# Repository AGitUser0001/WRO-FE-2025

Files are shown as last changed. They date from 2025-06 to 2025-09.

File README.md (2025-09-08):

# WRO-FE-2025
Our repository for the 2025 World Robot Olympiad - Future Engineers.

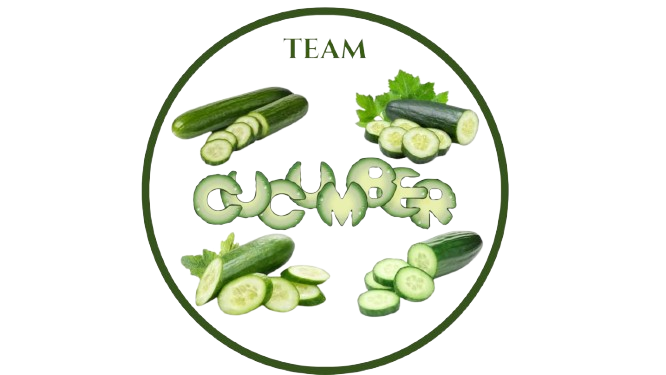
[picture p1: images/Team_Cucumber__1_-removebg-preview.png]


Team Name: Team Cucumber

This repository contains information about our robot and the building process. 

## Links
- [Building Instructions](/Building-Instructions.md)
- [Software Documentation](/Software-Documentation.md)
- [Open Challenge Documentation](/Software-Documentation.md#open-challenge)
- [Obstacle Challenge Documentation](/Software-Documentation.md#obstacle-management)

## Table of Contents
* [The Team](#team)
* [The Challenge](#challenge)
* [The Robot](#robot-image)
  * [First Design](#first)
  * [Final Design](#final)
* [Performance Videos](#video)
  * [Open challenge](#OPCV)
  * [Obstacle Challenge](#OBCV)  
* [Management](#management)
  * [Mobility Management](#mobility-management)
      * [Motor](#motor)
      * [Servo Motor](#servo-motor)
      * [Wheels](#wheels)
  * [Power and Sense Management](#power-and-sense-management)
    * [Battery](#battery)
    * [Raspi Camera](#camera)
    * [LiDAR](#lidar)
    * [Raspberry Pi 5](#pi)
    * [Expansion Board](#expansion-board)
    * [Circuit Diagram](#circuit-diagram)
* [Total Cost](#cost-report)
* [Future Potential Improvements](#potential-improvements)

## Team Members 

### Lucas Zheng
**Age:** 14

**Introduction:**
Hello, I'm Lucas, and this is my first time competing in WRO. I'm from Canada and 14 years old. I'm interested in coding and mathematics. It is my first year of high school at Donald A. Wilson Secondary School. I was interested in WRO Future Engineers because it has hardware and software aspects.
### Walter Wu
**Age:** 14

**Introduction:**
Hi, my name is Walter and I'm from Canada, this is my second WRO season, two years ago I participated in WRO Robo mission and ended up on the international stage in Panama. This year since I was old enough for future engineers I decided to sign up for a completely different challenge, I am currently 14 years old and I have many interests from coding to a variety of video games and sports, I will be attending All saints catholic secondary school for their AMP program.
### Eric Huang
**Age:** 15

**Introduction:**
Hello, I'm Eric, and I have already participated in two WRO competitions so far. Although I have not entered the international stage in any of them, I believe these competitions helped me better problem solve and gave me something to do. This is also why I am participating in Future Engineers this year. My interests are chess, badminton, and swimming. 
## Our coach

### Rice Rao
<table>
  <tr>
    <td width="50%" style="text-align: left;">
       
    </td>
    <td width="50%" style="text-align: left; vertical-align: top;">
      <h3>Achievements:</h3>
      <ul>
        <li>Head coach of Robotics Competitions including FLL (First LEGO League) Tournament and WRO (World Robotics Olympiad). Led teams in winning multiple national, international robotics and programming awards.</li>
        <li>Over 20 years of IT industry experience as software engineer working internationally.</li>
        <li>MSc in Electrical & Computer Engineering from University of Alberta.</li>
        <li>BSc in Mathematics from Peking University.</li>
      </ul>
    </td>
  </tr>
</table>

## Group photo
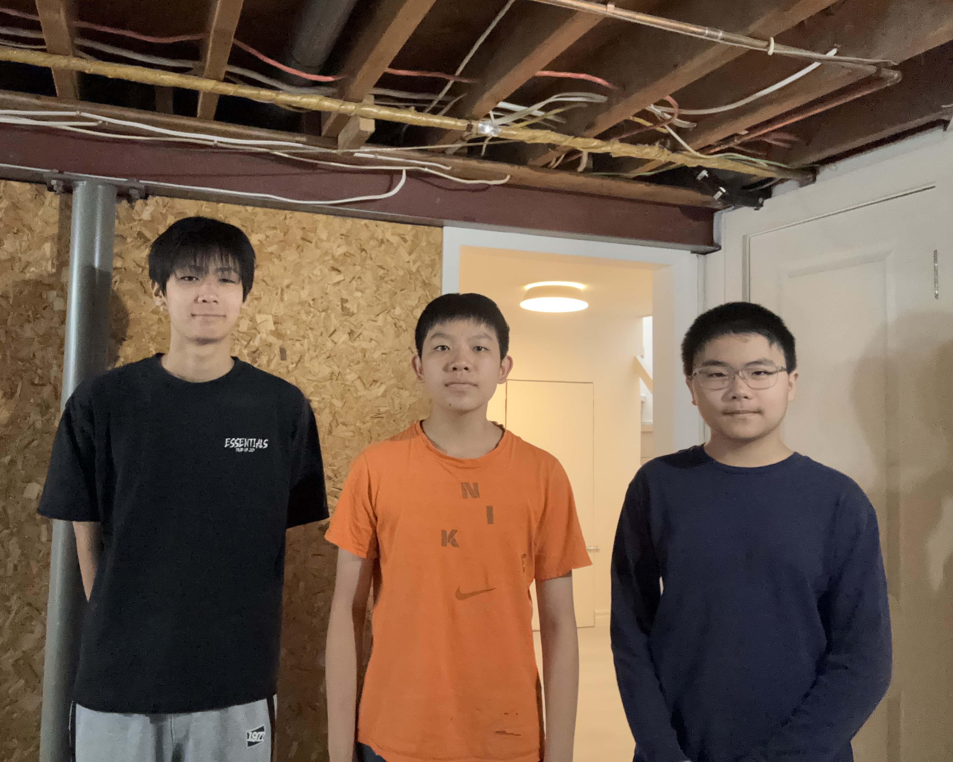
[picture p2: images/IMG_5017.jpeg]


## The Open Challenge 
The robot must complete three laps on the track after being placed randomly inside the walls of the track. The robot must have one button pressed to turn on the robot and one button pressed to run the program. After this, **no further interactions** with the robot are allowed.
## The Obstacle Challenge
The robot must complete three laps on the track with randomly arranged traffic signs which are green and red. The robot must go around the **right** side of a **red** pillar, and the **left** side of a **green** pillar. 

Learn about the challenges as well as the rules [here](https://wro-association.org/wp-content/uploads/WRO-2024-Future-Engineers-Self-Driving-Cars-General-Rules.pdf)

## Photos of Our Completed Robot: 

| *Front* | *Back* |
| :--: | :--: |
|  |  | 
| *Left* | *Right* |
|  |  | 
| *Top* | *Bottom* |
|  |  | 

## Our videos       

### Our video of the open challenge on [Youtube](https://youtu.be/A2_c18GIqZw) 

### Our video of the obstacle challenge on [Youtube](https://youtu.be/azQxvRrqnGA)

## First design 
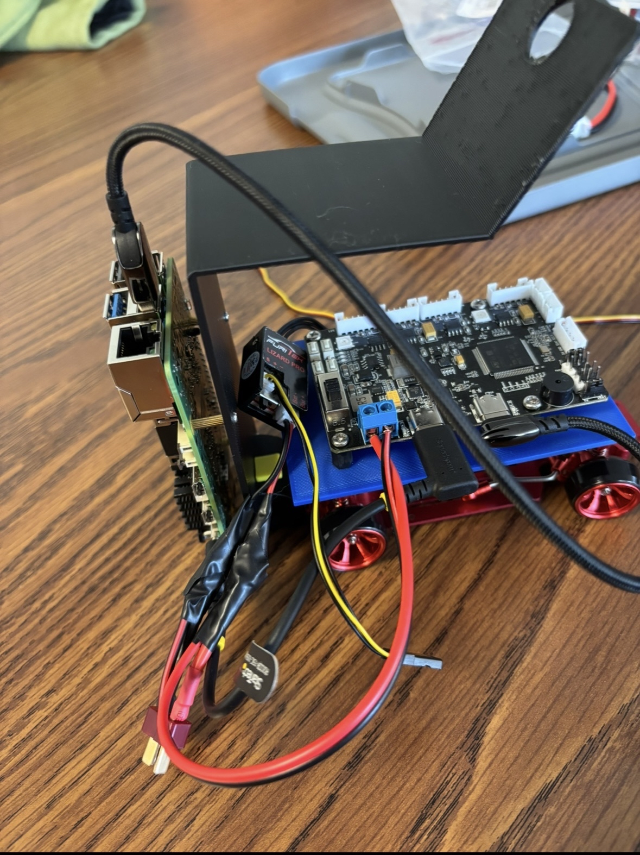
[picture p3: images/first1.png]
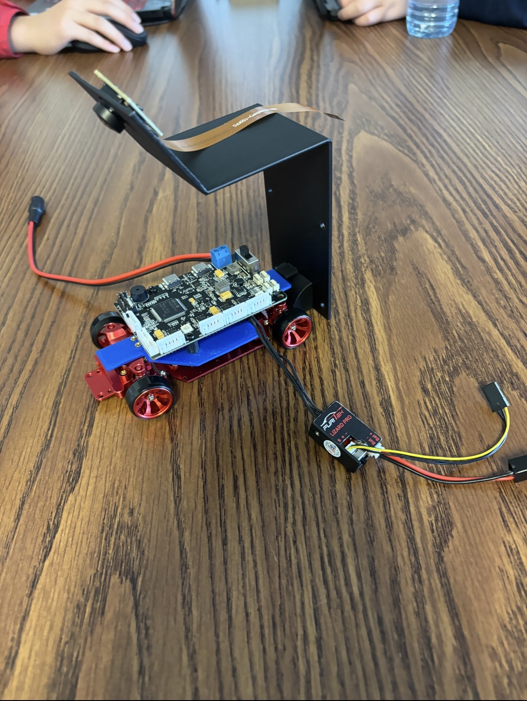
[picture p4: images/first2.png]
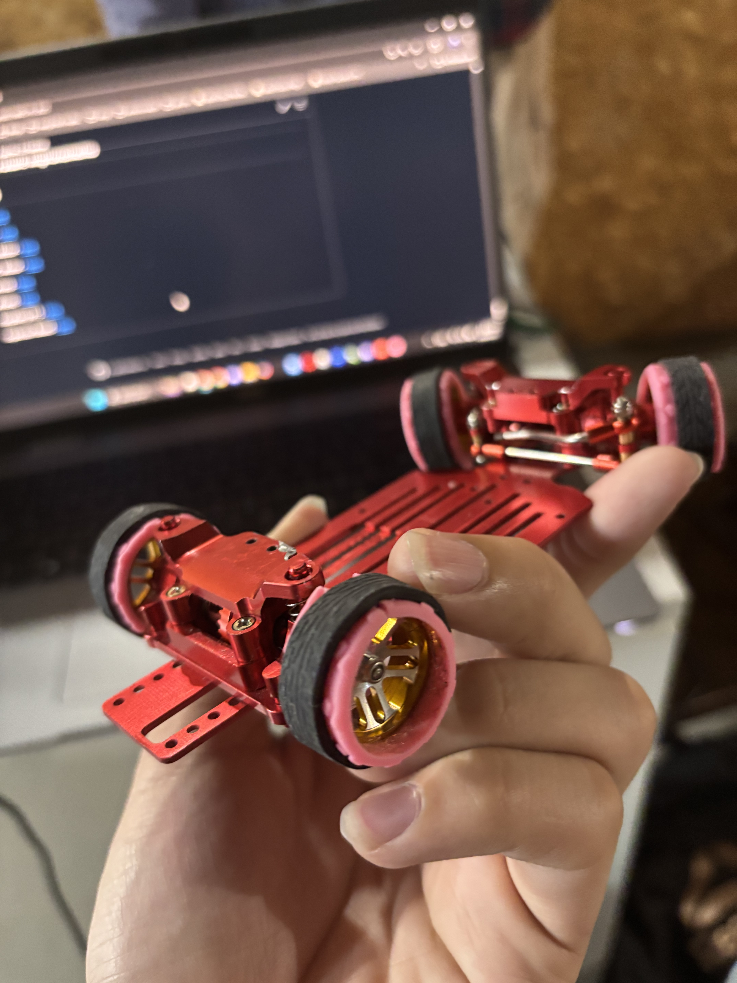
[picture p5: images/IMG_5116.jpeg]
   

Above are some pictures of our first design for our robot. As you can see there are many flaws and as well as components missing. Although these designs not quite what we needed, they helped us find inspiration for our eventual final design. In fact, we decided to keep a lot of ideas from our earlier generations to incorporate into our robot. One of such is that we have the Raspberry Pi mounted on the back instead of the usual where it is found on top the chassis. Our servo was mounted using tape at first, but we realized that it wasn't secure enough. We switched to Velcro, but we realized that the servo motor still wiggled around a little. We switched to a type of Velcro that snaps in place, but it was still moving. We never had much problem securing our motor, using a piece of metal that came with the metal chassis to secure it. Finally, our 3d printed mount was not stable enough and the plastic was not thick enough. Another thing we tried in the first design were adding tire grips, these grips ended up being too high maintenance and couldn't properly do their job so we switched to finding better wheels.

## Final Design 

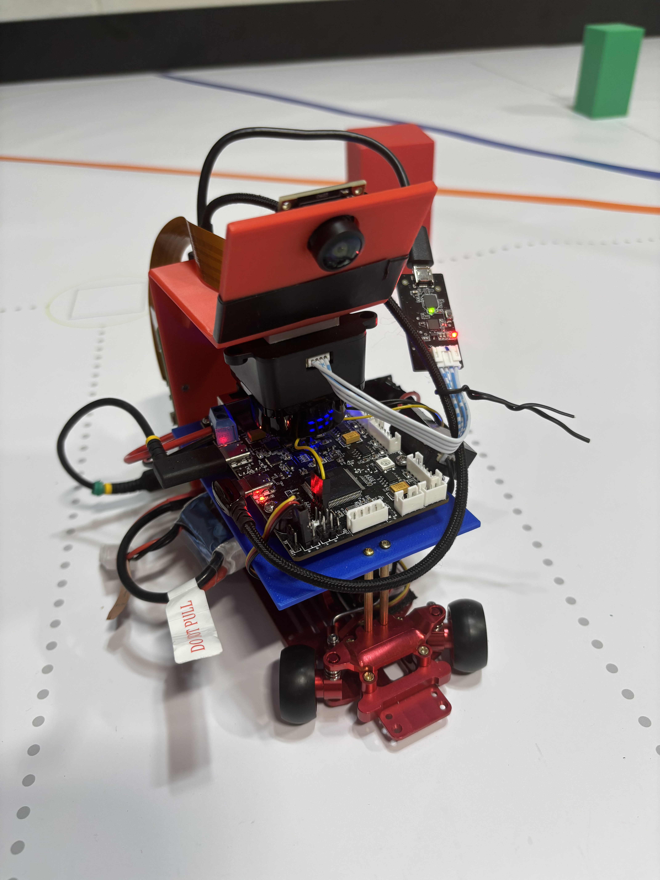
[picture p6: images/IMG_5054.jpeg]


Our final design has many improvements and additions than the previous versions. Our robot includes sensors, those being the LiDAR and a camera, motors; being the servo and BLDC motors, a raspberry pi 5 and expansion board, as well as wheels and a battery. Our robot has been made to be compact so that we can be efficient with our limited space on the 1/28 scale chassis. We raised the baseplate to make space for the battery and the servo motor. To secure the servo motor, we used tape with Velcro, finding that this was better than just tape or just Velcro. We also added triangular supports to the mount so that it can hold the extra weight of the LiDAR. We made the plastic of the mount thicker as well to support the camera, Raspberry Pi, and the LiDAR. We changed the pin so that it was more stable and better connected the mount to the metal chassis.

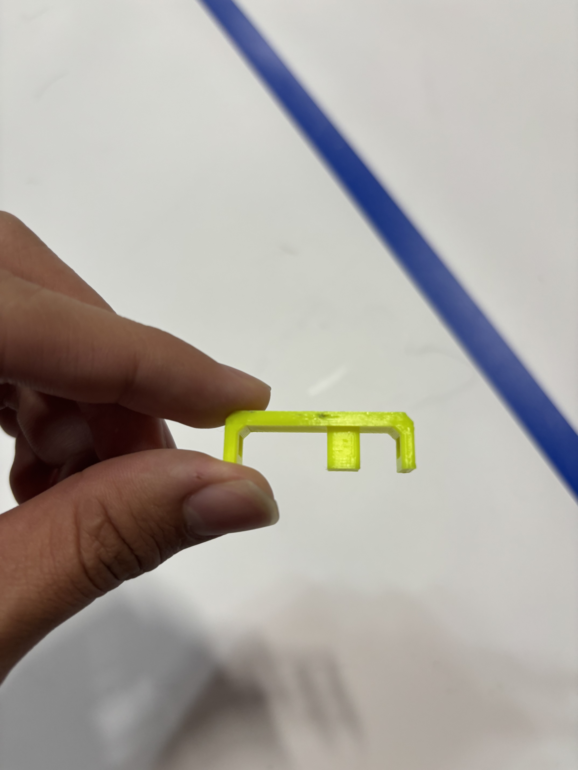
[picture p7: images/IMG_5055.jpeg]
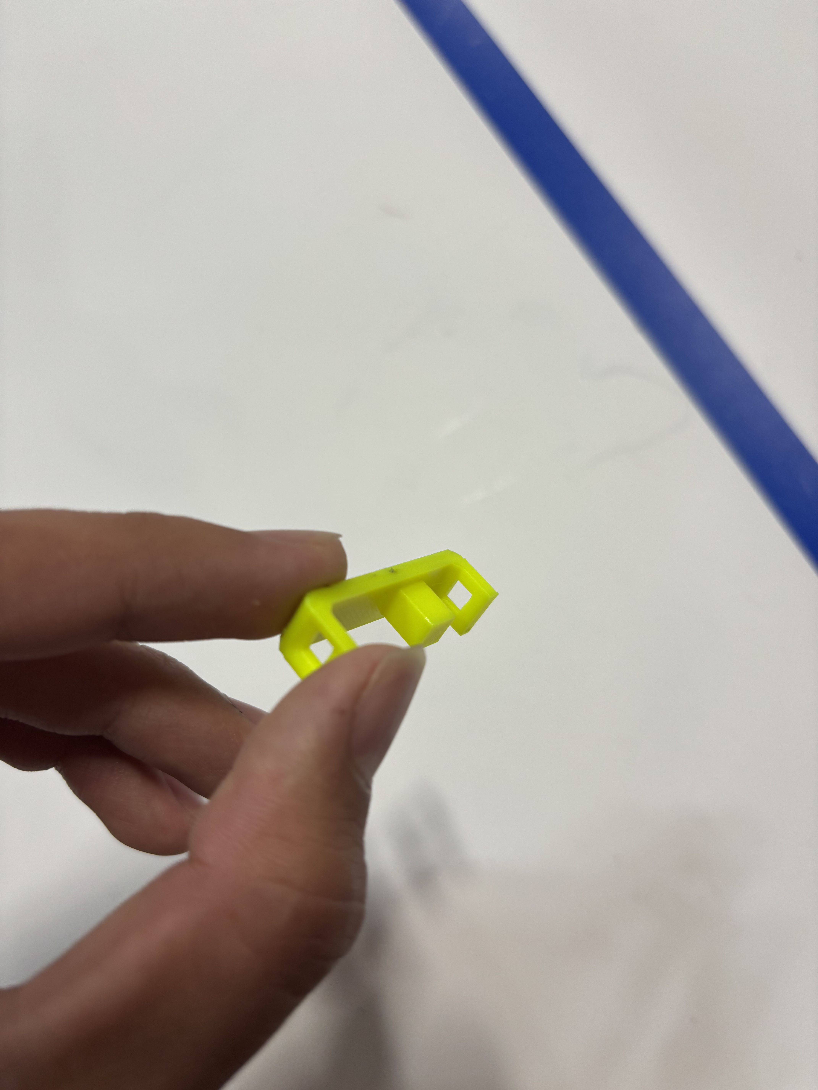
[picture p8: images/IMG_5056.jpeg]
 

## Challenges We Faced 
### Short Circuit
After we soldered the battery connector to the ESC and the extension board, we were ready to flip the switch. Unfortunately, we switched the positive and negative wires, resulting our extension board to be burned. This taught us to be more cautious before closing the circuit and helped us avoid similar situations along the way.
### Servo Motor
We realized that we could not fit the battery and the servo motor under our 3D printed plate. We decided to raise the 3D printed plate to make more space. 
A new problem came up. It was hard to fully secure the servo motor in place. 
### Processing Too Slow
We overcame the problem of our program running too slowly by switching to a combination of multiprocessing and threading. Initially, our single-threaded approach caused delays, especially when handling tasks like image processing, motor control, and sensor feedback all at once. To solve this, we implemented multiprocessing to separate heavy tasks, such as camera frame processing, into their own processes, allowing them to run in parallel without blocking the main loop. At the same time, we used threading for lighter background tasks like logging data or checking sensors continuously. This made our program significantly faster and more responsive, allowing our robot to perform in real time without lag or missed inputs.
### LiDAR Was Unreliable
At first, we used our mounted camera to follow walls. This worked out great for the open challenge and seemed to work well for our obstacle challenge at first, but we soon found some cases in which the robot would completely go the wrong way with our camera wall following and pillar detection.
### Unreliable Orange Line Detection
We switched to orange line detection from blue line detection because it was more reliable. However, when we tested it in a different lighting environment, it would sometimes find too many orange lines (it would detect red pillars as orange lines), or it would detect too little orange lines. This is still a problem, so in new environments our first thing to do will be to adjust the LAB values for the orange line and the two colors of the pillars.
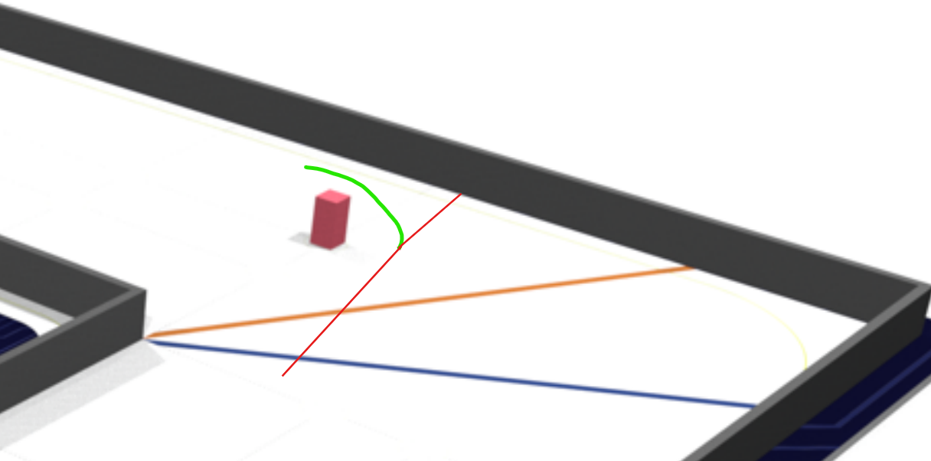
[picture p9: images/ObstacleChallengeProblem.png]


The robot sees this red pillar and tries to turn left, but as soon as it stops seeing it, the robot turns right. We thought using LiDAR for wall following would be a good solution since it can "see" very far. However, LiDAR was very unreliable, especially when the robot was in motion. This led to the robot wobbling around and sometimes just crashing into a wall. We went back to using our camera for wall following. 

# Management 

## Power and Sense Management 

Our power and sense management is made up of our battery, our camera, our LiDAR, Raspberry Pi 5, and our Hiwonder expansion board. The battery provides power to all of our components such as our motor, servo motor, camera, etc. We secured the battery using Velcro. It is placed right under the baseplate. We thought this spot would be best since it is near the center of the robot. Our camera is one of the most important parts of our robot. We use it for wall following and detecting the pillars. Our camera is mounted high so that the bottom of the robot does not get in its way. Our camera is then secured using electrical tape. We made sure that our camera had a large enough FOV so that it could see both walls. Our LiDAR was recently implemented. It is secured under the mount with double-sided tape. We use it for parking and detecting the parking walls. We decided to use the Raspberry Pi 5 as our microcontroller because it is stable and has a good amount of processing power. It is mounted with screws on the back of the mount. Finally, our expansion board provides us with more ports. All these components help the robot navigate the open and obstacle challenge. 

### Our battery 
<table>
  <tr>
    <td width="50%" style="text-align: left;">
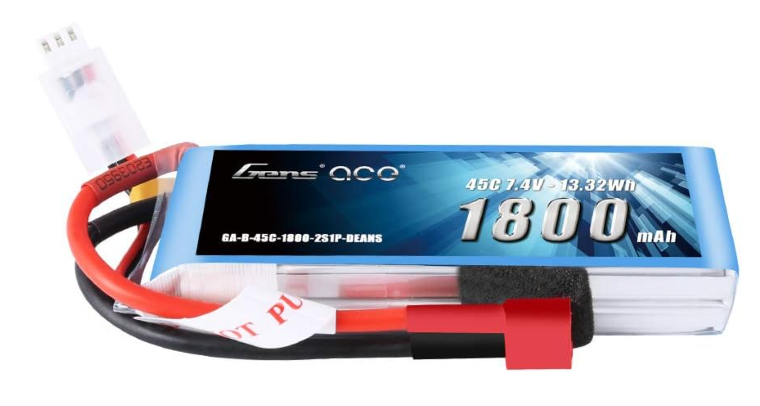
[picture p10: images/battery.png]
       
    </td>
    <td width="50%" style="text-align: left; vertical-align: top;">
      <h3>Specifications:</h3>
      <p>Voltage(V): 7.4V</p>
      <p>Capacity(mAh): 1800mAh</p>
      <p>Discharge rate(C): 90C</p>
      <p>Weight: 100g</p>
    </td>
  </tr>
</table>

### Potential Improvements
- We could have bought a battery with higher density energy cells to extend the operating time while generally having the same weight. 
- We could have made a special compartment to mount the battery instead of it hanging on the bottom of the baseplate. This would reduce the stress on the robot and prevent the battery from falling down.

### Our Camera 
<table>
  <tr>
    <td width="50%" style="text-align: left;">
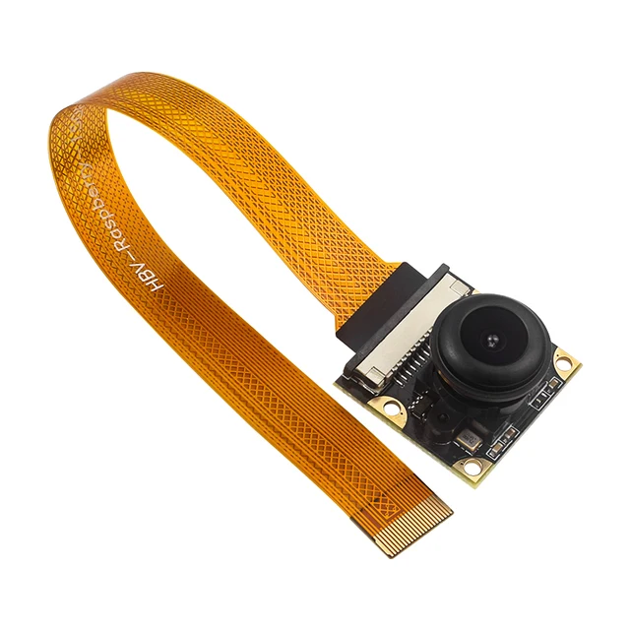
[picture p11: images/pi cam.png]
       
    </td>
    <td width="50%" style="text-align: left; vertical-align: top;">
      <h3>Specifications:</h3>
      <p>Sensor Size: 1/4-inch optical format (approx. 3.674 mm × 2.760 mm)</p>
      <p>Sensor Resolution: 3280 × 2464 pixels</p>
      <p>Pixel Size: 1.12 µm × 1.12 µm</p>
      <p>Lens Mount Type: M12 (S mount)</p>
      <p>Autofocus support: None</p>
    </td>
  </tr>
</table>

### Potential Improvements
- We could have swapped the camera lens with a higher quality lens to increase detection of pillars and to prevent colors getting mixed up.
- We could have adjusted our fish-eye lens so that it does not warp the shape of some objects.
  
### Our LiDAR 
<table>
  <tr>
    <td width="50%" style="text-align: left;">
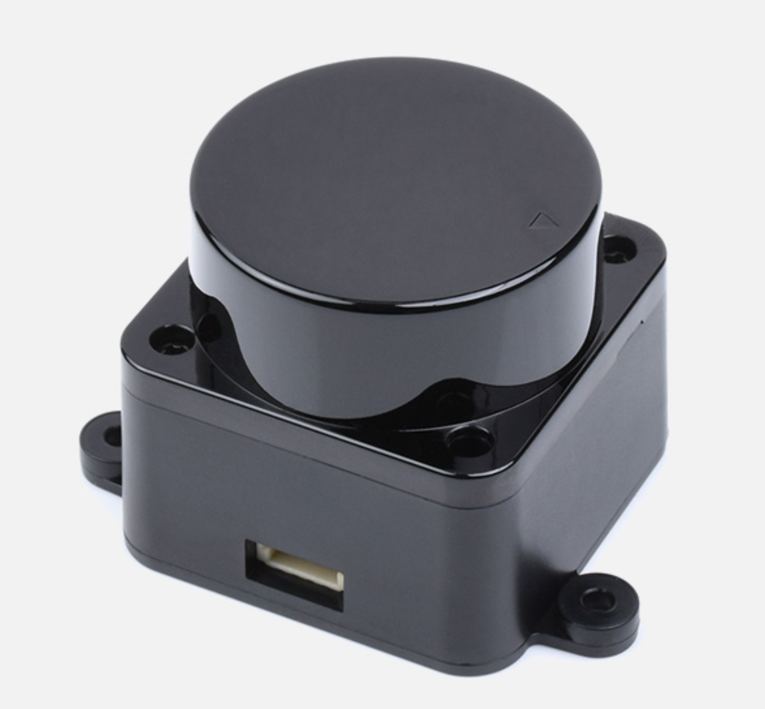
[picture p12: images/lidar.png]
       
    </td>
    <td width="50%" style="text-align: left; vertical-align: top;">
      <h3>Specifications:</h3>
      <p>Typical measuring range: 0.03~12m</p>
      <p>Scanning range:	360°</p>
      <p>Sampling frequency:	5000 Hz</p>
      <p>Scanning frequency:	10 Hz</p>
      <p>Angular resolution:	≤0.72°</p>
    </td>
  </tr>
</table>

### Potential Improvements
- We could have bought a LiDAR with a higher Hz/RPM so that it updates the scan faster.
- We could have bought a solid-state LiDAR. These have much higher frame rates and are more accurate. However, many of these are costly and they cannot see 360 degrees.
### Our Raspberry Pi 5 
<table>
  <tr>
    <td width="50%" style="text-align: left;">
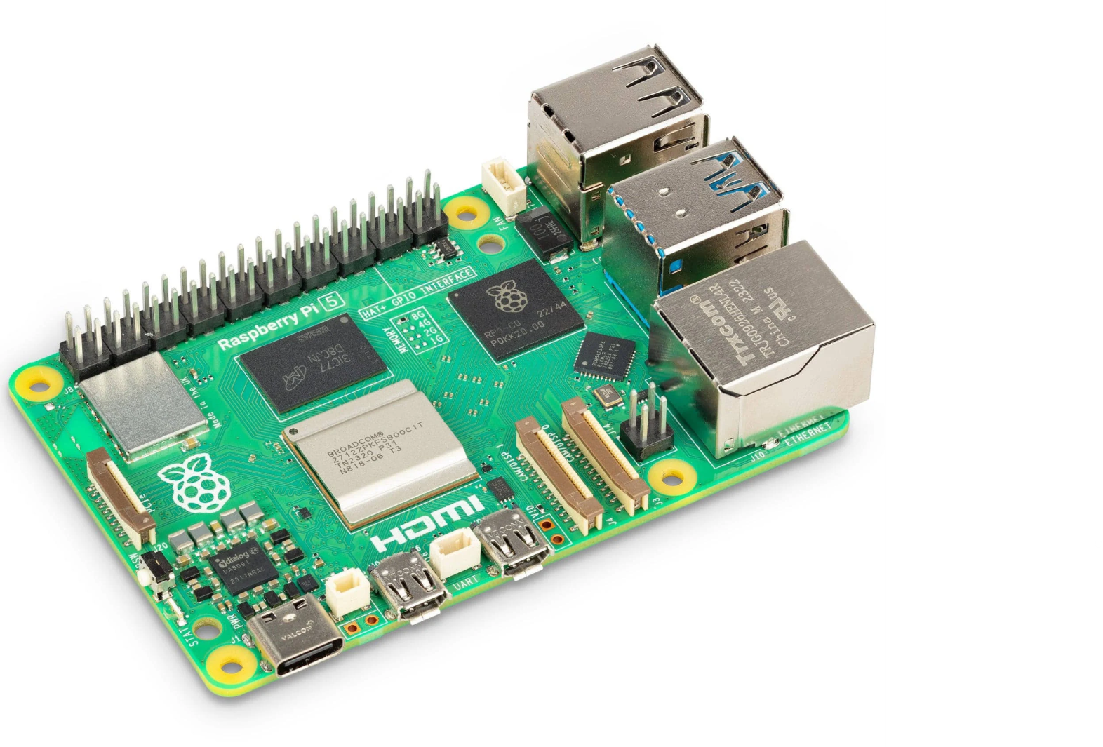
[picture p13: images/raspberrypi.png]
       
    </td>
    <td width="50%" style="text-align: left; vertical-align: top;">
      <h3>Specifications:</h3>
      <p>Processor (SoC): Broadcom BCM2712</p>
      <p>GPU: VideoCore VII</p>
      <p>RAM: 16 GB LPDDR4X-4267 MHz</p>
      <p>Storage: micro-SD (SDR104) + PCIe 2.0 x1 slot</p>
      <p>Power supply: 5 V / 5 A via USB-C</p>
    </td>
  </tr>
</table>

### Potential Improvements
Right now, the Raspberry Pi is mounted to the back piece with extra long screws and, for the future if we we're to try with this design again we would definitely like it to be closer as with the Raspberry Pi being farther out not only does it make our robot bigger, but as well it shifts the center of gravity and overall makes it harder to steer. With a combination of better wheels and a tighter place for the Raspberry Pi the robot could definitely perform better.
Another note to add for the future was that we should've definitely found more uses for the GPIO pins such as with an ultrasonic sensor.

### Our Expansion Board 
<table>
  <tr>
    <td width="50%" style="text-align: left;">
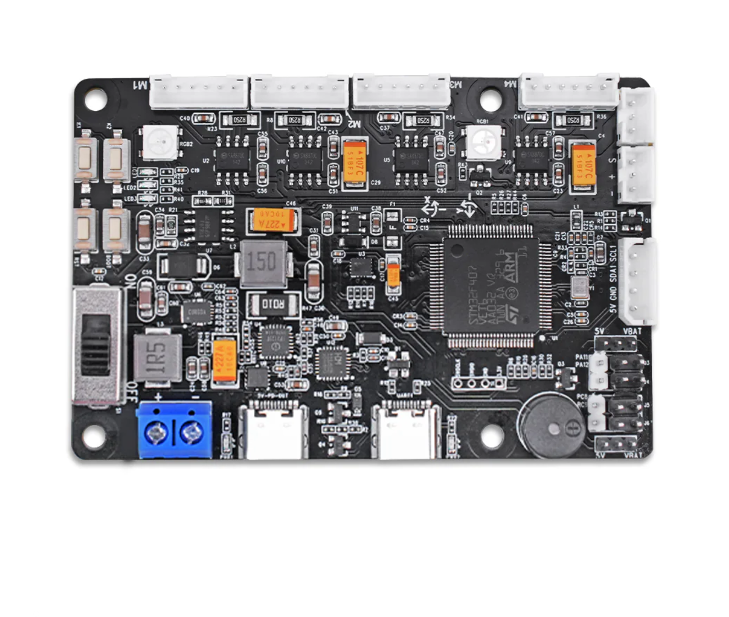
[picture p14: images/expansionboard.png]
       
    </td>
    <td width="50%" style="text-align: left; vertical-align: top;">
      <h3>Specifications:</h3>
      <p>Main Control Chip: STM32F407VET6</p>
      <p>PD Power Support: Raspberry Pi 5 protocol, up to 5 V / 5 A</p>
      <p>IMU Sensor: 6-axis (gyro + accelerometer)</p>
      <p>Connectivity: USB, I2C, sensor expansion, PWM/serial control</p>
      <p>Motor Ports: 4-channel encoder motors with PID control</p>
    </td>
  </tr>
</table>

### Potential Improvements
With our design as is, our expansion board is quite cluttered and the wires aren't properly managed very well. Next time we attempt something like this we would definitely aim to keep the wires short and make sure they aren't crossing into anything they shouldn't.
### Our circuit schematic [here](#diagram)

## Mobility Management 
Our mobility is made possible by a few different parts, these being the code that gets run through our raspberry pi and expansion board, the actual moving made possible through the BLDC motor and ESC, the steering which is controlled by our servo motor and can well, steer the front wheels, and our wheels. Firstly, our code is tuned so that the servo motor can steer precisely where we want it to, and so that the DC motor can move exactly as fast as we want it to. The next parts being our actual BLDC moto and ESC. The ESC is wired into our expansion board so that we can utilize PWM (pulse width modulation) to control how fast our BLDC motor is and our BLDC motor runs into a differential gear at the back of our car as we decided to use RWD instead of FWD or AWD because well, the servo is controlling the front wheels and AWD is banned. 
Next is our servo motor. Our servo motor is wired directly into the PWM pins on our expansion board and the servo arm is attached to our front wheels, the servo motor required a lot of fine tuning as the servo_straight variable was hard to decide. Lastly our wheels went through many variations before finally settling on the one we are using currently. Before as the tires were too small we would add tire grips to increase the circumference of the tires as well as the grip as sometimes they would slip, but those tire grips would often fall off decreasing the consistency of our robot, so after careful consideration we landed on the current version of wheels which worked really well during testing.

### Our BLDC Motor 
Our DC brushless motor drives the back wheels thanks to the differential gear which ensures that the car can drive straight. Our motor is secured using a metal part of the chassis that is secured with screws. We chose motor because it is small, reliable, and the gear ratio matched with the chassis gears.
<table>
  <tr>
    <td width="50%" style="text-align: left;">
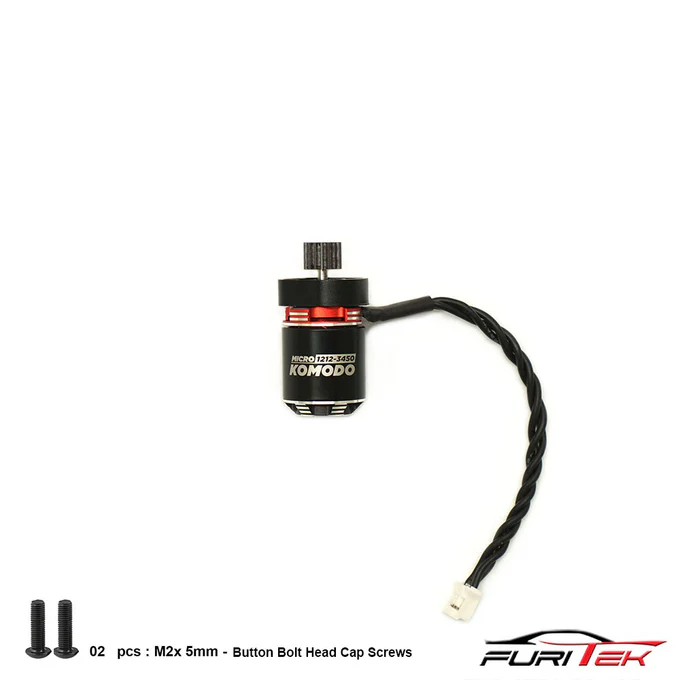
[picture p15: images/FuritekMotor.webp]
       
    </td>
    <td width="50%" style="text-align: left; vertical-align: top;">
      <h3>Specifications:</h3>
      <p>Voltage: 10V</p>
      <p>Gear Ratio: 1:2</p>
      <p>Speed: 3450 rpm</p>
      <p>Weight: 17.5g</p>
    </td>
  </tr>
</table>

### Potential Improvements
Our BLDC motor is connected to a standard gear but, the gears we are using are made out of plastic and are easily broken, as this has happened if the past and it caused our robot to stutter or stop moving completely. We could've found an alternative to plastic gears such as a lightweight metal or even just a stronger plastic alternative as in nylon.

### Our Servo Motor 

<table>
  <tr>
    <td width="50%" style="text-align: left;">
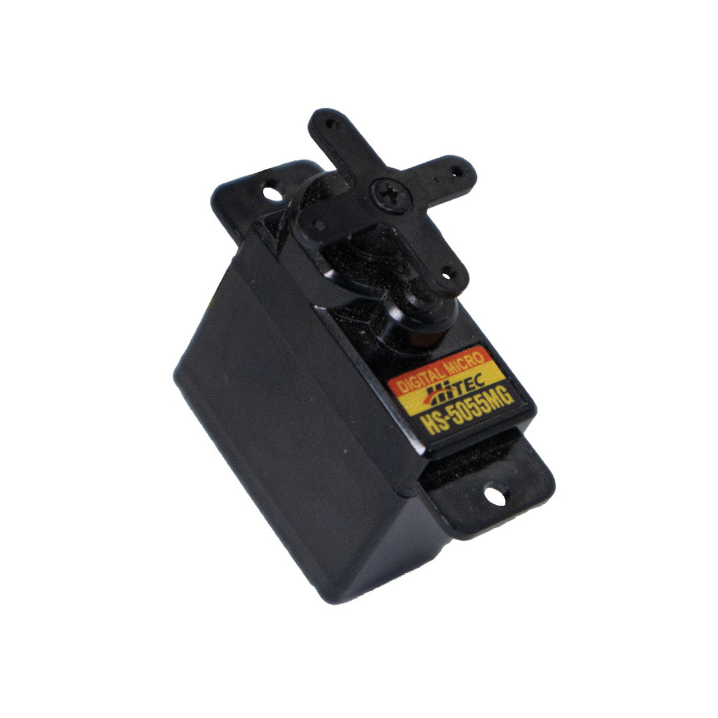
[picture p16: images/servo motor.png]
       
    </td>
    <td width="50%" style="text-align: left; vertical-align: top;">
      <h3>Specifications:</h3>
      <p>Operating Voltage Range: 4.8V ~ 6.0V</p>
      <p>Speed: 2.0 ~ 1.7</p>
      <p>Maximum Torque Range kg. / cm.: 1.3 ~ 1.6</p>
      <p>Weight: 9.5g</p>
    </td>
  </tr>
</table>

### Potential Improvements
Our servo motor is slightly prone to moving from a lot of wear. This can offset the servo arm and make our steering slanted. In the future if we were to attempt the same thing we would 100% find a way to secure the servo in place such as, with super glue or zip ties.

### Our Wheels 
<table>
  <tr>
    <td width="50%" style="text-align: left;">
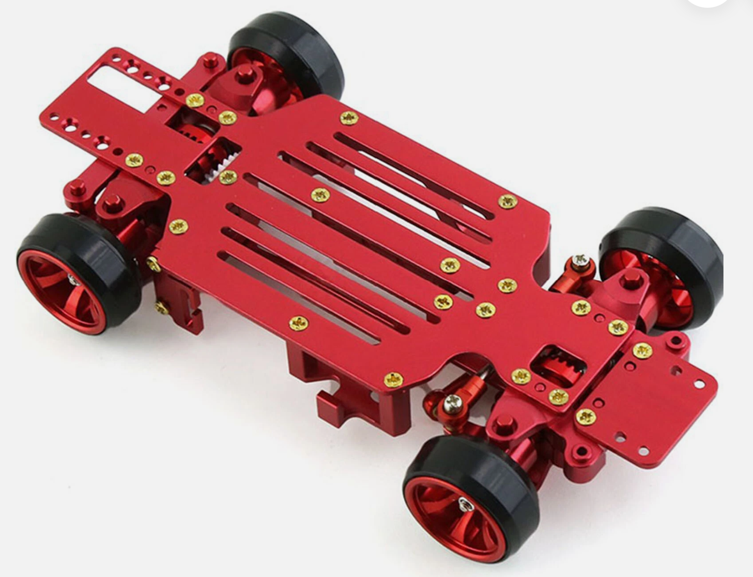
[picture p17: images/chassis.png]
       
    </td>
    <td width="50%" style="text-align: left; vertical-align: top;">
      <h3>Specifications:</h3>
      <p>Diameter w/o tires: 20mm</p>
      <p>Width w/o tires: 8mm</p>
      <p>Weight: 16g</p>
    </td>
  </tr>
</table>

### Potential Improvements
Our wheels are small and it causes our chassis to be lower to the ground causing it to occasionally brush against the mat, in more severe cases getting stuck. We could've browsed for bigger and more grippy wheels which would in turn solve this problem. 

### Circuit Diagram  


## Total Price of the Robot 
| Component  | Cost |
| --- | --- |
| Motor  | $110.51 |
| Servo Motor  | $24.99  |
| Camera  | $16.87  |
| Raspberry Pi 5  | $113.95  |
| 3D Printings  | $8  |
| Raspberry Pi Expansion Board | $54.98  |
| Metal Chassis  | $86.38  |
| Battery  | $42.78  |
| Wires  | $26.75  |
| Wheels  | $9.13  |
| Switch  | $1.03  |
| Velcro and Tape  | $21.30  |
| LiDAR sensor  | $89.99  |
| Total Price Before Tax | $606.66  |
| Total Price | $685.53  |

## Potential Future Improvements 
We should have added an automatic color correction calibration, as our camera has some problem adapting to different environments. Sometimes we would have to manually fine-tune the color correction for different lighting environments. Sometimes our environments would be too dark, leading the robot to wrongly detect certain things such as missing some green or red pillars. We could calibrate the color correction by holding up the red and green pillars, and recording and automatically adjusting the CIELAB values. 

We could add a voltage regulator to see when our robot is at low battery. Many of the problems in our obstacle and open challenge is caused by low battery and the readings from our sensors are less reliable when we have low battery. With this voltage regulator, we could avoid spending too much time trying to fix problems when instead they could be fixed by using a battery with full power. 

## Sources
LiDAR - [here](https://www.waveshare.com/wiki/D500_LiDAR_Kit)

Battery - [here](https://www.amazon.ca/Gens-ace-Battery-Airplane-Helicopter/dp/B073RFHKWH)

Servo Motor - [here](https://hitecrcd.com/hs-5055mg-economy-metal-gear-feather-servo/)

BLDC Motor - [here](https://furitek.com/products/combo-of-furitek-lizard-pro-30a-50a-brushed-brushless-esc-for-axial-scx24-with-bluetooth)

Camera - [here](https://www.aliexpress.com/item/1005007274396582.html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)

Wheels - [here](https://www.aliexpress.com/item/1005004174366878.html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,scm-url:1007.40196.394786.0,pvid:dbe58872-1796-4911-95bf-a4c5d060e85a,tpp_buckets:668%232846%238113%231998&pdp_ext_f=%7B%22order%22%3A%22162%22%2C%22eval%22%3A%221%22%2C%22sceneId%22%3A%2230050%22%7D&pdp_npi=4%40dis!CAD!5.81!5.81!!!28.73!28.73!%402101c59817427507077044104ec0d6!12000028283974218!rec!CA!!ABX&utparam-url=scene%3ApcDetailBottomMoreOtherSeller%7Cquery_from%3A)

Raspberry Pi 5 - [here](https://www.raspberrypi.com/products/raspberry-pi-5/)

Expansion Board - [here](https://www.hiwonder.com/products/rrc-lite)

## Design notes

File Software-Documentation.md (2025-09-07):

# Software Documentation

## Open Challenge
The goal of the open challenge is to make three laps around the track without touching any of the walls. For the open challenge, we use the camera as our only sensor. When one wall disappears, the robot turns that way. We use two ROIs (Region of Interests) to find the area of the left wall and the right wall. One is a wide rectangle on the left and the other is parallel. If there is a big enough difference between the area of both walls, the robot adjusts accordingly. We achieve the wall following by using PD (Proportional-Derivative) steering. The error is multiplied by our Kp value, then the last error is calculated then multiplied by our Kd value. These values added up tells the robot how much to steer. 

To make sure we stop after three laps, the robot detects the blue line. We use an ROI located in the middle of the screen to detect the blue line. For a complete detection, the robot first must see the blue line from a distance, then up close, and finally, the blue line must be out of the camera's sight. After twelve detections, the robot waits and then stops.

## Obstacle Management
The goal of the obstacle challenge is roughly the same as the open challenge with added obstacles, not only do you have to make three laps around the track without touching any of the walls you have to do it while avoiding preplaced traffic lights where the colour of the traffic lights determines what side you pass it on, for example if the colour is green then you pass on the left, and if the colour is red you'll have to pass on the right. In addition to the rules previously mentioned the robot also has a optional added difficulty of parking, where there is a parking lot added to the track in which the robot starts and has to end in while being parallel to the wall.

We finished the obstacle challenge by first making a wall follow code so that our robot would be able to run through the circuit, next we made it so that our camera would be able to tell what colour each traffic light was and therefore what side to pass it on, after our robot figures out what colour each traffic light is, it then turns so that the traffic light is far enough on the left or right side of the camera so that the robot wouldn't ram into it. After this it then tries to go back to the centre of the track and occasionally turns depending on if the traffic light is on the corner or not. Since wall follow with just a camera isn't very reliable on obstacle challenge due to the added traffic lights, we implemented a LiDAR sensor which helps keep track of walls put also helps with parking. The logic behind how we figure out the three laps are up is the same, we count how many blue lines we pass thus connecting to how many corners we've passed. 
### Pillar Detection
```py
class ObstacleChallengeProcess():
  lower_red = np.array([35, 150, 124])
  upper_red = np.array([140, 255, 255])
  lower_green = np.array([80, 0, 124])
  upper_green = np.array([190, 107, 255])
```
```py
      _, _, MaxRedArea, _, _, red_x, _, red_y =self.detect_contours(ROI_front_LAB, self.lower_red, self.upper_red, draw_image=display_ROI_front, c_colour=(0, 0, 255), conditional=ROI_front_LAB[:, :, 1] > ROI_front_LAB[:, :, 2])
      =
      _, _, MaxGreenArea, _, _, green_x, _, green_y =self.detect_contours(ROI_front_LAB, self.lower_green, self.upper_green, draw_image=display_ROI_front, c_colour=(0, 255, 0))
```

```py
def detect_contours(self, img_lab, lower_lab, upper_lab, threshold = 500, draw_image = None, *, conditional=None, filterSolids=True, draw_bounding_box=True, draw=1, c_colour=None, b_colour=None):
    mask = cv2.inRange(img_lab, lower_lab, upper_lab)
    if conditional is not None:
      mask = cv2.bitwise_and(mask, conditional.astype(np.uint8) * 255)
    contours, _ = cv2.findContours(mask, cv2.RETR_EXTERNAL, cv2.CHAIN_APPROX_SIMPLE)
    if filterSolids: contours = list(filter(self.filterSolids, contours))
    center_x = 0
    center_y = 0
    bottom_y = 0
    cntList, MaxCnt, MaxCntArea, approx, bounding_box = processContours(contours, threshold, draw_image, draw_bounding_box=draw_bounding_box, draw=draw, c_colour=c_colour, b_colour=b_colour)
    if MaxCnt is not None:
      x, y, w, h = bounding_box
      center_x = x + w / 2
      center_y = y + h / 2
      bottom_y = y + h
    return cntList, MaxCnt, MaxCntArea, approx, bounding_box, center_x, center_y, bottom_y
```
### Parking Wall Detection

```py
  lower_magenta = np.array([0, 155, 63])
  upper_magenta = np.array([140, 255, 130])
```

```py
def parking(self, ROI_front_LAB, display_ROI_front, rw, rh, status, error_pillar, stopped, parking_detected, parking_side, last_parking_detect):
    limit = 500
    magenta1center_x = rw / 2
    magenta1center_y = rh / 2
    magenta1bottom_y = rh / 2
    magenta2center_x = rw / 2
    magenta2center_y = rh / 2
    magenta2bottom_y = rh / 2
    current_error = 0
```
```py
    cntList, _, _, _, _, _, _, _ =self.detect_contours(ROI_front_LAB, self.lower_magenta, self.upper_magenta, limit, draw_image=display_ROI_front, draw=2)
    maxCnts = getMaxContours(cntList, 2)
    (maxCnt1, MaxMagentaArea1) = maxCnts[0] if len(maxCnts) > 0 else (None, 0)
    if maxCnt1 is not None:
      _approx, (x, y, w, h) = getBoundingBox(maxCnt1)
      magenta1center_x = x + w / 2
      magenta1center_y = y + h / 2
      magenta1bottom_y = y + h
    (maxCnt2, MaxMagentaArea2) = maxCnts[1] if len(maxCnts) > 1 else (None, 0)
    if maxCnt2 is not None:
      MaxMagentaArea2 = cv2.contourArea(maxCnt2)
      _approx, (x, y, w, h) = getBoundingBox(maxCnt2)
      magenta2center_x = x + w / 2
      magenta2center_y = y + h / 2
      magenta2bottom_y = y + h
```

## Our code explained

### Python libraries
For open challenge:
cv2  ros_robot_controller_sdk  time  numpy  picamera2  utils

For obstacle challenge:
ctypes  numpy  picamera3  time  ros_robot_controller_sdk  cv2  multprocessing  threading  queue  lidar  ObstacleChallengeProcess  utils

For ObstacleChallengeProcess:
numpy  math  cv2  time  queue  utils

For IMU:
subprocess  threading  math  multiprocessing

For LiDAR:
serial  struct  threading  multiprocessing  numpy  multiprocessing shared_memory  queue  time  cv2

For Utils:
Cv2  numpy  time

### LiDAR 
```py
BAUD = 230400
PACKET_HEADER = 0x54
PACKET_LEN = 47

DATA_TYPE = np.float32
DATA_SIZE = np.dtype(DATA_TYPE).itemsize
DATA_RES = 3

NUM_POINTS = 360 * DATA_RES
NUM_VALUES = 6

class LiDAR:
  def __init__(self, shm_name='lidar', port="/dev/ttyAMA0"):
    self.shm_name = shm_name

    try:
      self.shared_memory = shared_memory.SharedMemory(create=True, size=NUM_POINTS*NUM_VALUES*DATA_SIZE, name=shm_name)
    except FileExistsError:
      self.shared_memory = shared_memory.SharedMemory(name=shm_name)

    self.lidar_array = np.ndarray((NUM_POINTS, NUM_VALUES), dtype=DATA_TYPE, buffer=self.shared_memory.buf)
    self.stopped = multiprocessing.Value('b', False)
    self.lock = multiprocessing.Lock()

    self.process = multiprocessing.Process(target=LiDARProcess, args=(\
      port, self.stopped, shm_name, self.lock), daemon=True)
    self.process.start()

    self.__visualizer_display_queue = None
    self.__visualizer_lidar_roi_queue = None
    self.__visualizer_thread = None
```

### Camera
1. Camera Initialization and Configuration:
The camera is initialized and configured in the cameraThread function. The Picamera2 library is used to interact with the camera.

```py
picam2 = Picamera2()
picam2.configure(
  picam2.create_video_configuration(
    main={"size": (640, 480), "format": "RGB888"},
    sensor={"output_size": (1640, 1232)}
  )
)
picam2.start()
```

This part of the code configures our video stream with a main output resolution of 640x480 pixels and a sensor output of 1640x1232 pixels. Next, picam2.start() begins the camera's video capture.

2. Image Capture and Processing
Within the main loop of the cameraThread, the camera continuously captures images resulting in our video.

```py
while not stopped.value:
  frame = picam2.capture_array("main")
  with frame_lock:
    global_frame = frame
```

The picam2.capture_array("main") function captures a single frame from the camera's main stream and stores it in the frame variable. This frame is then copied to the global_frame variable, which is shared with other parts of the code for further processing.

3. Sending Data
A specific region of interest is also extracted from the captured frame and sent to another process via a multiprocessing queue.

```py
roi_for_process = frame[front_coords[1] : front_coords[3], front_coords[0] : front_coords[2]]
if not roi_queue.full():
  roi_queue.put(roi_for_process)
```

This section of code takes a subsection of the captured video, the roi, and places it into the roi_queue. This allows another process (ObstacleChallengeProcess) to access this specific part of the image for its own analysis without needing access to the entire frame.

### Steering
The core of the steering control is in the main loop of the wallFollowThread. The code first processes images to determine a steering error and then uses a PID controller to calculate the steering value for the servo motor.

```py
def wallFollowThread(stopped, enter_parking, error_pillar, status):
  global wallFollow_display

  ServoChannel = 4
  MotorChannel = 1
  ServoSpeed = 0.01
  MotorTransitionSpeed = 0.1
  MaxRightArea = 0
  MaxLeftArea = 0
  Kp = 0.1
  Kd = 0.04
  Ki = 0
  i_error = 0
  stMode = False
  stMode_time = -1
  error = 0
  last_error = 0
  threshold = 60

  board = rrc.Board()
  motorPW = 1615
  parkMotorPW = 1625
  servoStraight = 1800
  servoPW = servoStraight
  steer = 0
  rate_limit = 1/60
  avg_dt = rate_limit
  last_time = -1
  last_servoPW = -1

  def setMotor(motorPos):
    board.pwm_servo_set_position(MotorTransitionSpeed, [[MotorChannel, motorPos]])

  def setServo(servoPos):
    board.pwm_servo_set_position(ServoSpeed, [[ServoChannel, servoPos]])
    
  parking = Parking()
  parking_stage = None

  direction = 0
  was_obstacle = False
  first_frame = True
  last_status = b"FORWARD"

  wall_detect_line = ((int(640 / 2), 220), (int(640 / 2), 360))
  wall_detect_timer = {}

  parking_detect_line_left = ((190, 190), (0, 320))
  parking_detect_line_front = ((320, 190), (320, 320))
  parking_detect_line_right = ((450, 190), (640, 320))

  lower_magenta = np.array([35, 110, 0])
  upper_magenta = np.array([160, 255, 108])

  def findContours(image, draw_image=None, *, draw=1, c_colour=None, b_colour=None):
    contours, _hierarchy = cv2.findContours(image, cv2.RETR_EXTERNAL, cv2.CHAIN_APPROX_SIMPLE)
    cntList, MaxCnt, MaxCntArea, _approx, _bounding_box = processContours(contours, 200, draw_image, draw=draw, c_colour=c_colour, b_colour=b_colour)
    return cntList, MaxCnt, MaxCntArea

  setServo(servoPW)
  time.sleep(1)

  setMotor(1500)

  try:
    while not stopped.value:
      
      cur_time = time.time()
      if cur_time - last_time < rate_limit:
        time.sleep((last_time + rate_limit) - cur_time)
      cur_time = time.time()
      dt = cur_time - last_time
      if global_frame is None:
        continue
      last_time = cur_time
      avg_dt = (avg_dt * 0.95) + (dt * 0.05)

      with frame_lock:
        img = global_frame.copy()

      ROI_left = img[230:250, 0:300]
      ROI_right = img[230:250, 340:640]

      img_grey = cv2.cvtColor(img, cv2.COLOR_BGR2GRAY)
      _, img_grey_thresh = cv2.threshold(img_grey, threshold, 255, cv2.THRESH_BINARY_INV)
      ROI_left_thresh = img_grey_thresh[230:250, 0:300]
      ROI_right_thresh = img_grey_thresh[230:250, 340:640]
      cv2.rectangle(img, (0, 230), (300, 250), (255, 0, 0), 2)
      cv2.rectangle(img, (340, 230), (640, 250), (255, 0, 0), 2)

      _leftCntList, _MaxLeftCnt, MaxLeftArea = findContours(ROI_left_thresh, ROI_left, c_colour=(255, 0, 0), b_colour=(0, 0, 255))

      _rightCntList, _MaxRightCnt, MaxRightArea = findContours(ROI_right_thresh, ROI_right, c_colour=(255, 0, 0), b_colour=(0, 0, 255))

      current_error_pillar = -error_pillar.value
      if current_error_pillar != 0:
        if not was_obstacle:
          was_obstacle = True
        error = current_error_pillar
      else:
        if was_obstacle:
          was_obstacle = False
        error = MaxLeftArea - MaxRightArea

      if current_error_pillar == 0:
        steer = Kp * error + Kd * derivative + Ki * i_error if abs(error) > 0 else 0
        if stMode:
          steer = 200 * direction
      else:
        steer = current_error_pillar

      steer = min(300, max(-300, steer))
      servoPW = servoStraight + int(steer)
      
      if servoPW != last_servoPW:
        setServo(servoPW)
      last_servoPW = servoPW
      
  finally:

    setMotor(1500)
    parking.last_stage()
    print("WallFollow Thread Stopped")
```
The error variable is calculated as MaxLeftArea - MaxRightArea. If there's an obstacle, this value is overridden by error_pillar.value, which comes from the ObstacleChallengeProcess. This calculated error is then fed into a PD controller using the proportional gain Kp = 0.1 and derivative gain Kd = 0.04. The output of this controller is the steer value, which is then used to set the servo's pulse width. The setServo() function sends the final command to the physical servo, moving the wheels to steer the robot.

### Moving
The robot's forward and backward movement is controlled by the setMotor function, which sets the pulse width for the motor channel.

board.pwm_servo_set_position(MotorTransitionSpeed, [[MotorChannel, motorPos]]): This command is used to set the speed of the robot.

motorPW = 1615: This variable sets the standard pulse width for forward movement.

parkMotorPW = 1625: This variable sets the pulse width for forward movement during the parking sequence.

setMotor(1500): A pulse width of 1500 is used to stop the motor.

The if last_status != status: block controls the robot's direction and speed based on the status multiprocessing value (e.g., "FORWARD", "BACKWARD", "FORWARD_SLOW").

```py
def setMotor(motorPos):
    board.pwm_servo_set_position(MotorTransitionSpeed, [[MotorChannel, motorPos]])

cur_status = status.value
if last_status != status:
    if cur_status == b'BACKWARD':
        setMotor(1500)
        time.sleep(0.05)
        setMotor(1500 + (1500 - motorPW))
    elif cur_status == b'FORWARD':
        setMotor(motorPW)
    elif cur_status == b'FORWARD_SLOW':
        setMotor(motorPW - 5)
    elif cur_status == b'BACKWARD_SLOW':
        setMotor(1500)
        time.sleep(0.05)
        setMotor(1500 + (1500 - motorPW) + 5)
    last_status = status
```
This code block shows how the motor's position is adjusted to achieve forward, backward, and slow movement by changing the motorPos value passed to the setMotor function.

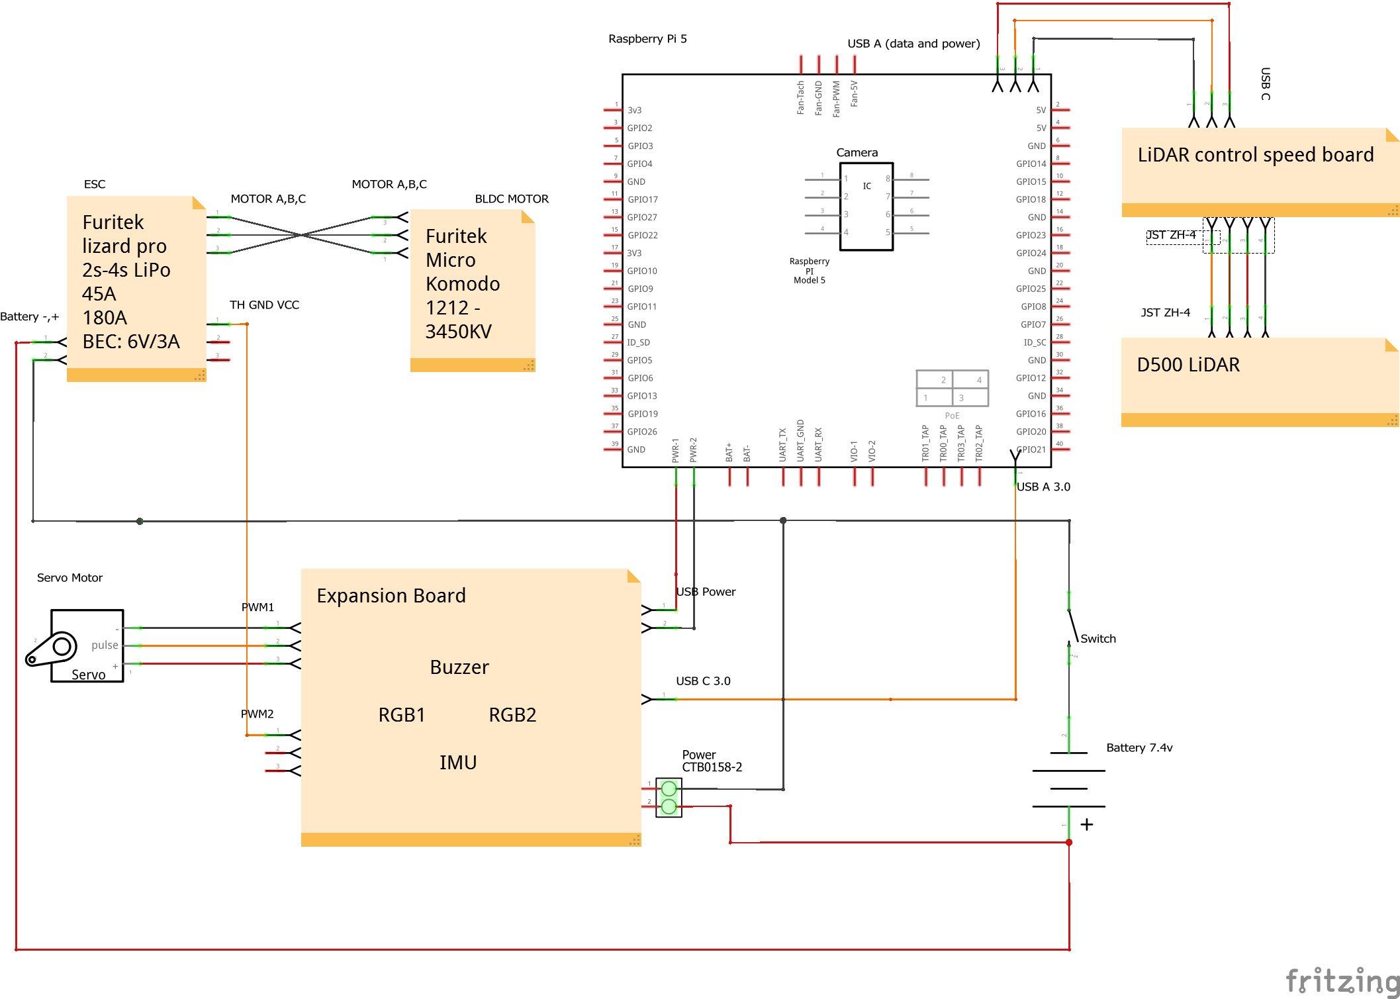
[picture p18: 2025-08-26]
images/wro schematic circuit_schem.png

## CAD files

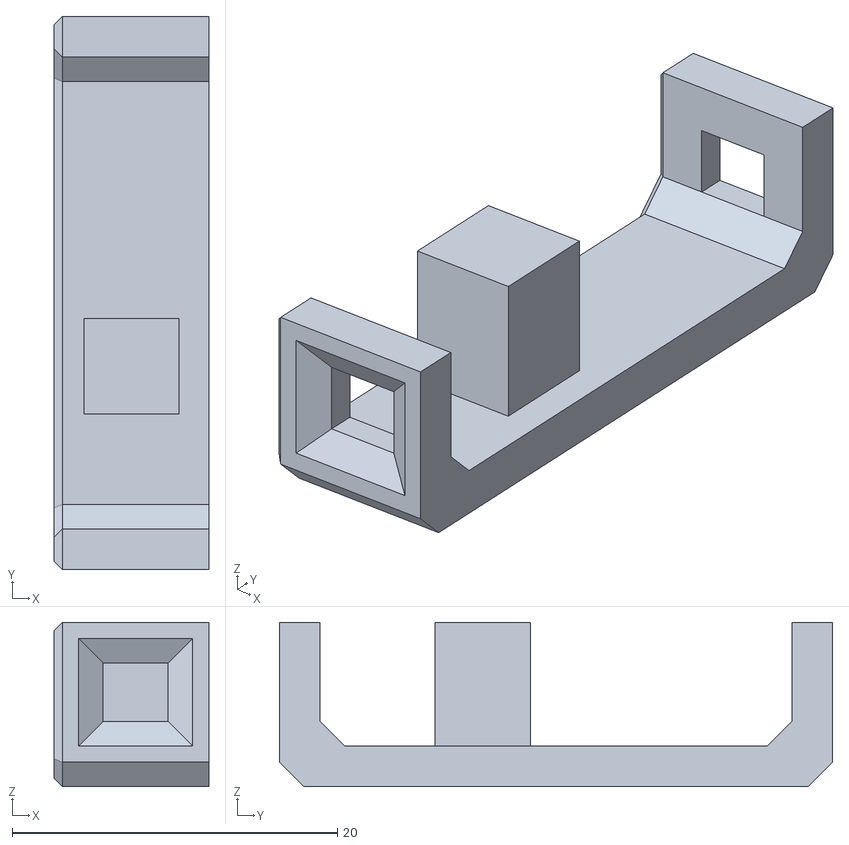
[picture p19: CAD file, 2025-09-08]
3d-prints/Pin @x9.5.stl
9.50 x 34.0 x 10.1

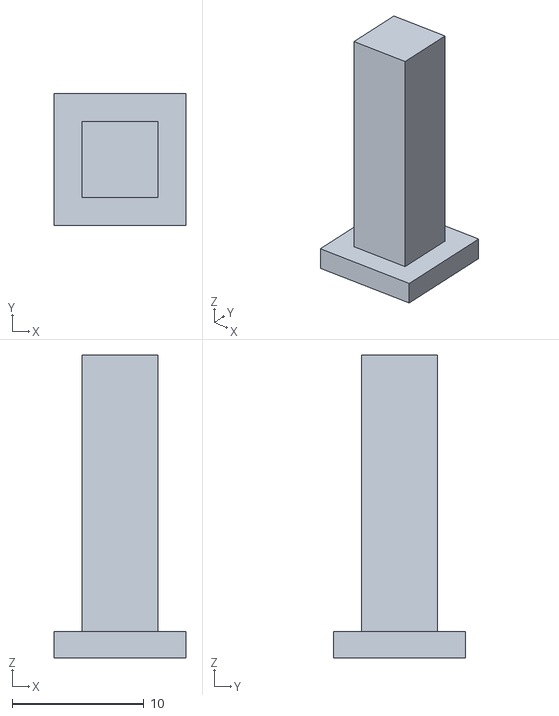
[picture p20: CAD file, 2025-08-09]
3d-prints/Pin Testing/Pin .575cm.stl
10.0 x 10.0 x 23.0

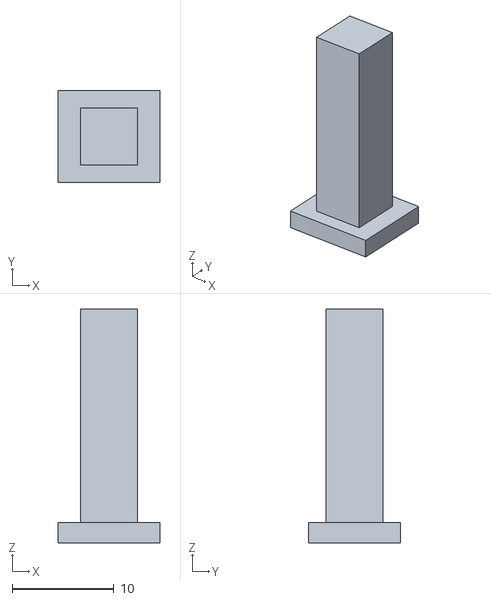
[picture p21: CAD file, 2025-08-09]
3d-prints/Pin .565cm.stl
10.0 x 9.00 x 23.0

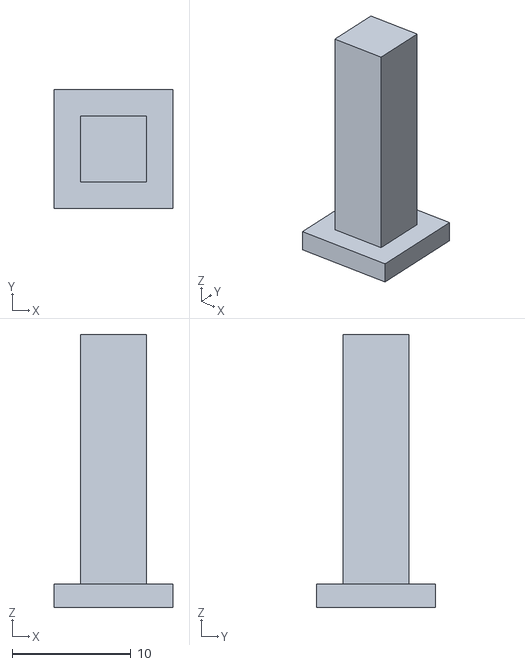
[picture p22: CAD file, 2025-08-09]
3d-prints/Pin Testing/Pin .56cm.stl
10.0 x 10.00 x 23.0

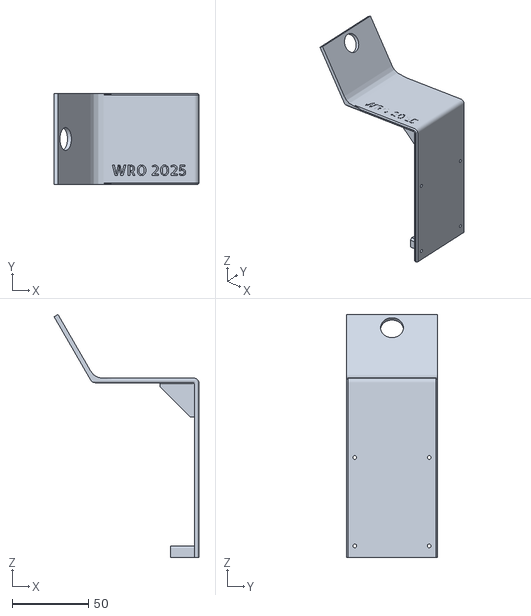
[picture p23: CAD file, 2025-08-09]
3d-prints/Mount x9.stl
95.0 x 60.0 x 159.4

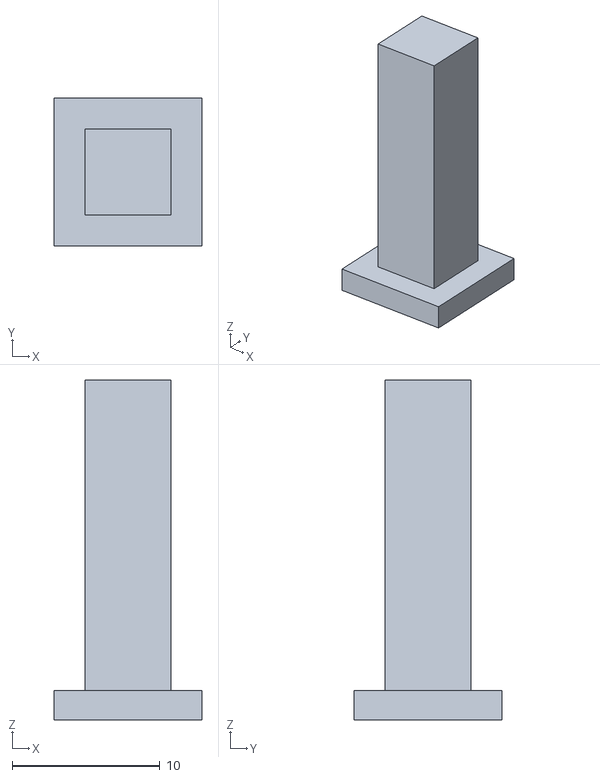
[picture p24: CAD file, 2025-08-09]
3d-prints/Pin Testing/Pin .58cm.stl
10.0 x 10.00 x 23.0

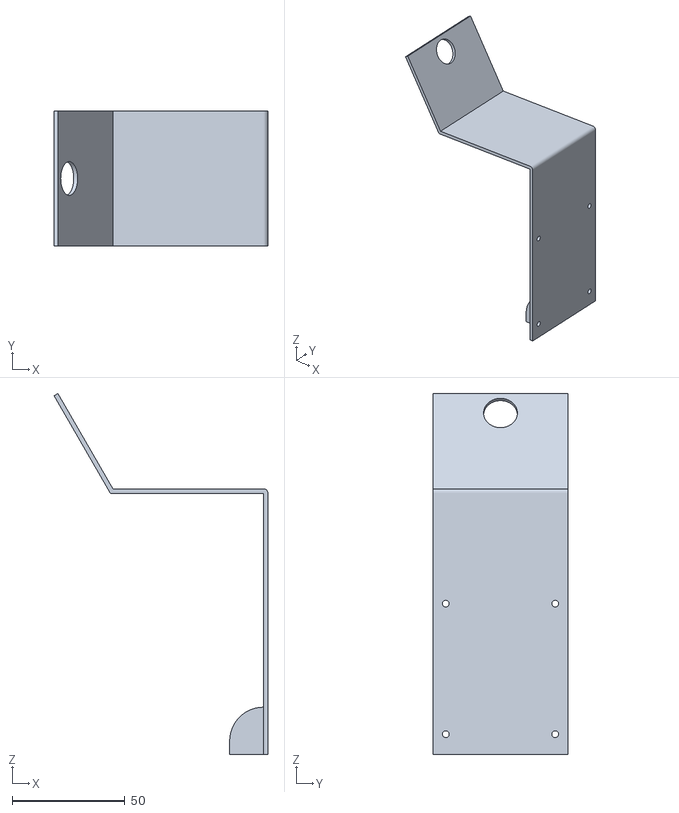
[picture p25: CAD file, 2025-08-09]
3d-prints/Mount x4.stl
95.0 x 60.0 x 160.3

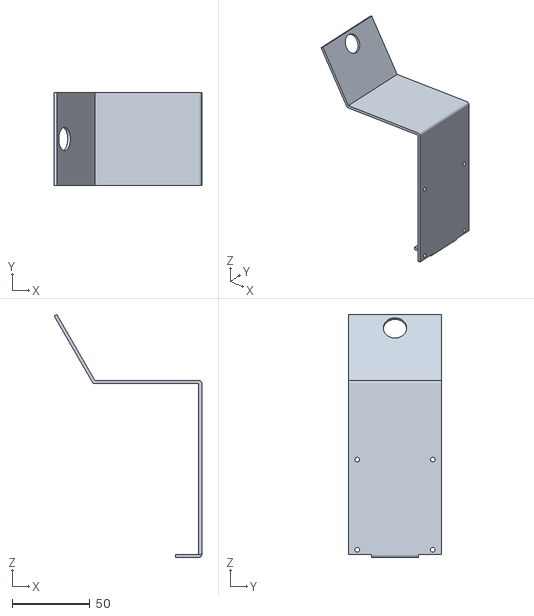
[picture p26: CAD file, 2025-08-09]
3d-prints/Mount x1.stl
95.0 x 60.0 x 156.3

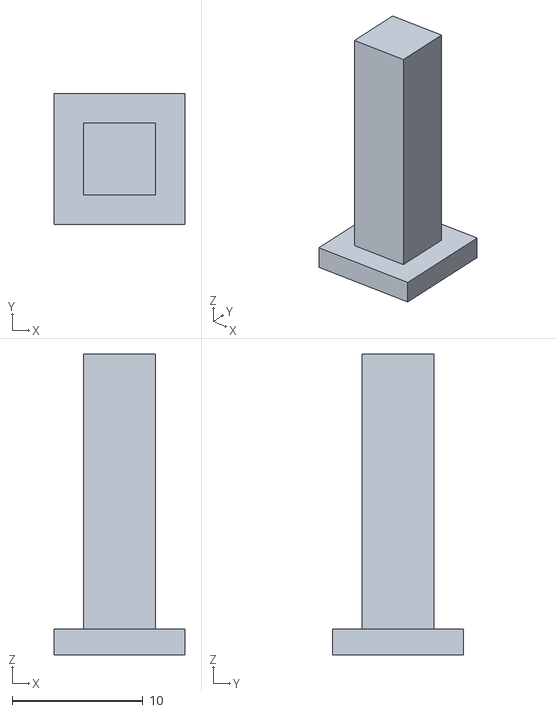
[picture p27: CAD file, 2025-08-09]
3d-prints/Pin @x3.stl
10.0 x 10.0 x 23.0

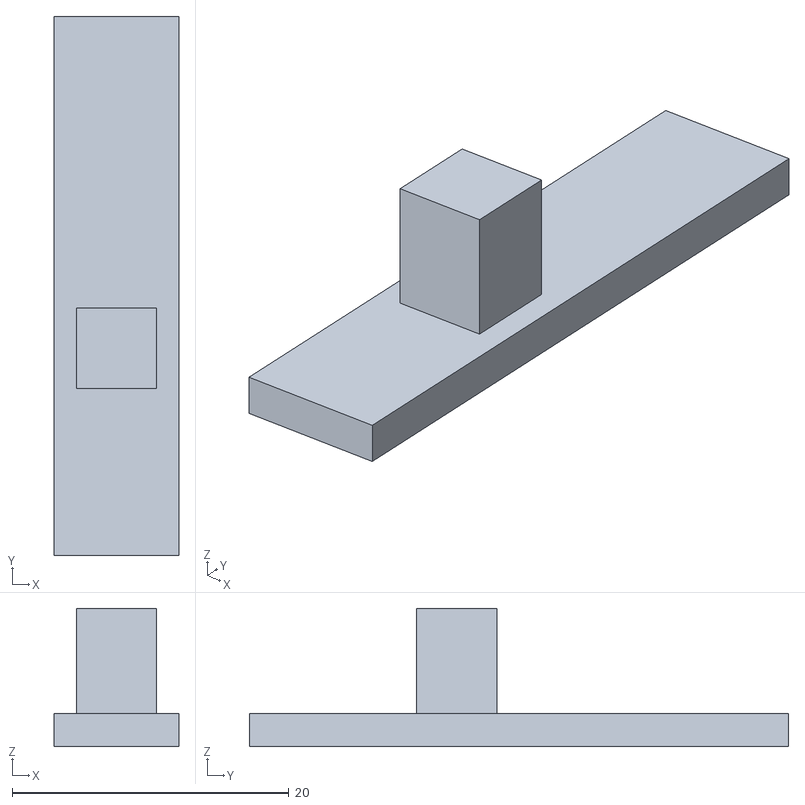
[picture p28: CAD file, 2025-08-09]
3d-prints/Pin @x9.stl
9.00 x 39.0 x 10.0

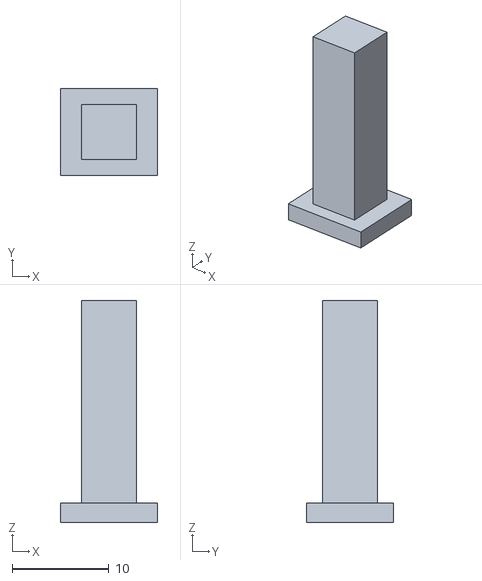
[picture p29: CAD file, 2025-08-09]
3d-prints/Pin @x7.stl
10.00 x 9.00 x 23.0

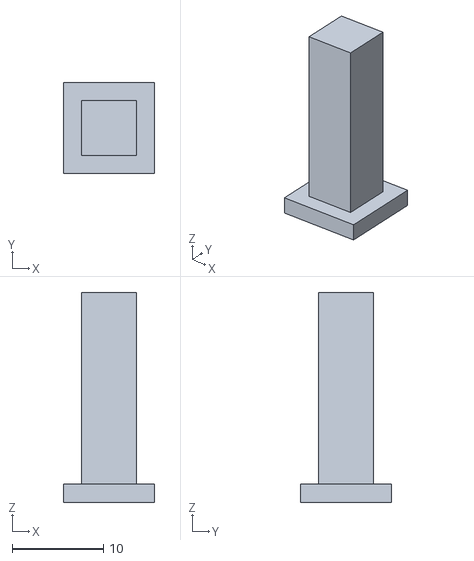
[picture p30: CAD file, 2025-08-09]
3d-prints/Pin @x2.stl
10.0 x 10.0 x 23.0

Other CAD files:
3d-prints/Pin Testing/Pin .565cm.stl
3d-prints/Pin Testing/Pin .57cm.stl
3d-prints/Mount x8.stl
3d-prints/Mount x6.stl
3d-prints/Mount x5.stl
3d-prints/Mount x7.stl
3d-prints/Baseplate v4.stl
3d-prints/Baseplate v5.stl
3d-prints/Baseplate v6.stl
3d-prints/Baseplate v7.stl
3d-prints/Baseplate v8.stl
3d-prints/Baseplate v9.stl
3d-prints/Mount x2.stl
3d-prints/Mount x3.stl
3d-prints/Part v0.stl
3d-prints/Part v1.stl
3d-prints/Part v2.stl
3d-prints/Part v3.stl
3d-prints/Pillar.stl
3d-prints/Pin @x5.stl
3d-prints/Pin @x6.stl
3d-prints/Pin @x8.stl

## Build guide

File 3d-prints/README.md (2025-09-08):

# 3D Prints
This is a table, in chronological order, that lists the timeline of 3D prints.

| Part | Version | |
| --- | --- | --- |
| [Part](Part%20v0.stl) | v0 | not printed |
| [Part](Part%20v1.stl) | v1 | printed, didn't fit, cut off some parts. screw holes too small. |
| [Part](Part%20v2.stl) | v2 | printed |
| [Part](Part%20v3.stl) | v3 | not printed, needed screw holes |
| [Baseplate](Baseplate%20v4.stl) | v4 | printed, printer was bad. |
| [Mount](Mount%20x1.stl) | x1 | printed, base broke off, realized screws didn't work for this |
| [Baseplate](Baseplate%20v5.stl) | v5 | printed, changed to allow motor to fit, needed larger holes for mounting ROS extension board. |
| [Baseplate](Baseplate%20v6.stl) | v6 | printed, but plate is now lifted, so many parts now unnecessary |
| [Mount](Mount%20x2.stl) &[Pin](Pin%20@x2.stl) | x2 | printed, tolerances too tight for pin hole, slight measurement problems |
| [Mount](Mount%20x3.stl) &[Pin](Pin%20@x3.stl) | x3 | printed, pin too loose, mount holes for raspberry pi too big |
| [Pins](Pin%20Testing/) | Testing | printed, .6 perfect |
| [Baseplate](Baseplate%20v7.stl) | v7 | printed, kinda curved |
| [Mount](Mount%20x4.stl) | x4 | printed, print failure |
| [Baseplate](Baseplate%20v8.stl) | v8 | printed, holes misaligned |
| [Mount](Mount%20x5.stl) &[Pin](Pin%20@x5.stl) | x5 | printed, pin disappeared, holes for raspberry pi misaligned |
| [Pin](Pin%20.565cm.stl) | .565cm  | printed, too loose |
| [Baseplate](Baseplate%20v9.stl) | v9 | printed, very good |
| [Mount](Mount%20x6.stl) &[Pin](Pin%20@x6.stl) | x6 | printed, needs some fixes |
| [Mount](Mount%20x7.stl) &[Pin](Pin%20@x7.stl) | x7 | printed, could be more tight |
| [Mount](Mount%20x8.stl) &[Pin](Pin%20@x8.stl) | x8 | printed, connection slot too tight |
| [Mount](Mount%20x9.stl) &[Pin](Pin%20@x9.stl) | x9 | printed, mount is good, pin could be improved |
| [Pin](Pin%20@x9.5.stl) | x9.5 | printed, very good |

Versions are unique across parts. Parts can have subparts, which are listed
after an ampersand.\
Final versions: [Baseplate v9](Baseplate%20v9.stl), [Mount x9](Mount%20x9.stl),
[Pin @x9.5](Pin%20@x9.5.stl)

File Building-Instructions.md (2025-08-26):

# Building Instructions
The construction of our robot is split up into 11 steps. Step zero being to first print our 3d prints which can be found in our 3d prints folder. Step one being to modify the chassis and soldering. Step two being to next gather all the required parts and components. Step 3 is to attach the 3d prints. Step four is to start the build by attaching the movement parts. Step five is to wire everything together. Step six is to add the sensors. Step seven is attaching the battery. Step eight is soldering the switch. Step nine to finish the build with final touches. Finally, step ten to import the code and run it.

***Step Zero:***
This step is purely dedicated to acquiring the 3d prints. You will need to find the prints in the 3d prints folder on our repository, next download them and print them out, if you are unsure on how to you can always use external help such as Google or Youtube.

***First step:***
This step is to alter your chassis to become fit for our build with a series of modifications. These being first to take out the long beam on the top which is connected to the front and rear gear boxes as it is in the way, and then secondly to take out the servo housing.

**1.**

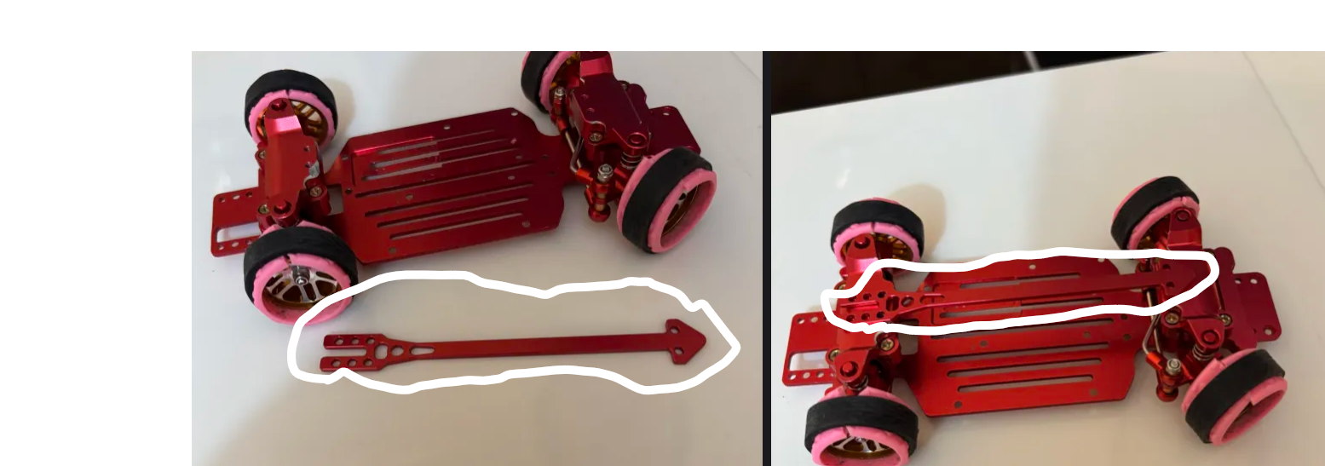
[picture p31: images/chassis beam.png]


**2.**

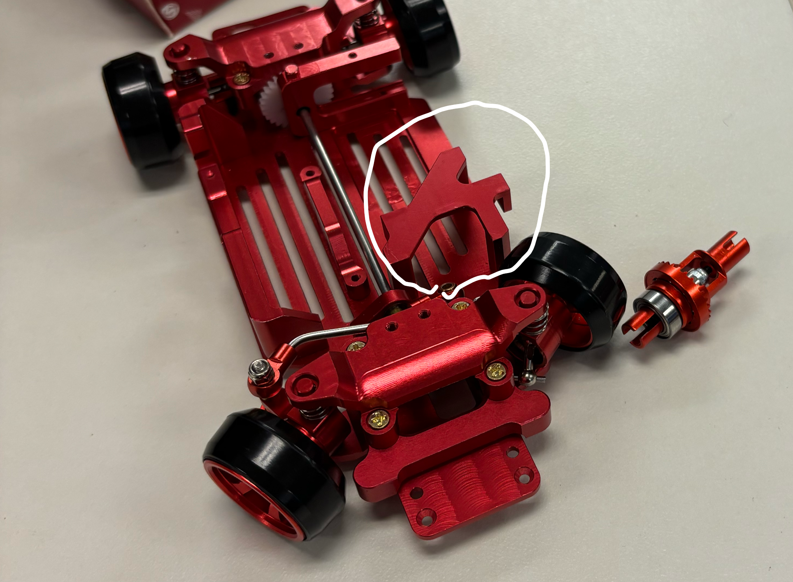
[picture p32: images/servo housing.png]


As well, this step includes soldering a wire and switch. You will need to solder a switch to a wire as well as making it have one input and two outputs, the input will be from the battery and the outputs will be into the expansion board and into the ESC for the BLDC motor.

***Second step:***
You need to gather all the parts and components for our robot, those which are listed before when we calculated the total cost of our robot. These components are a BLDC motor, a servo motor, a camera, Rasberry Pi 5, all of our 3d prints, the expansion board, our chassis, battery, wires,  switch, Velcro, tape, and electrical tape.

***Third step:***
Attaching the 3d prints. The baseplate is to be screwed in on top of the chassis with screws and extra long screw extensions, and the back part which should slide into the very back of the chassis along with the stopper that you put in through the top of the of the bottom of the backplate, there is a hole made for it.

**Baseplate**

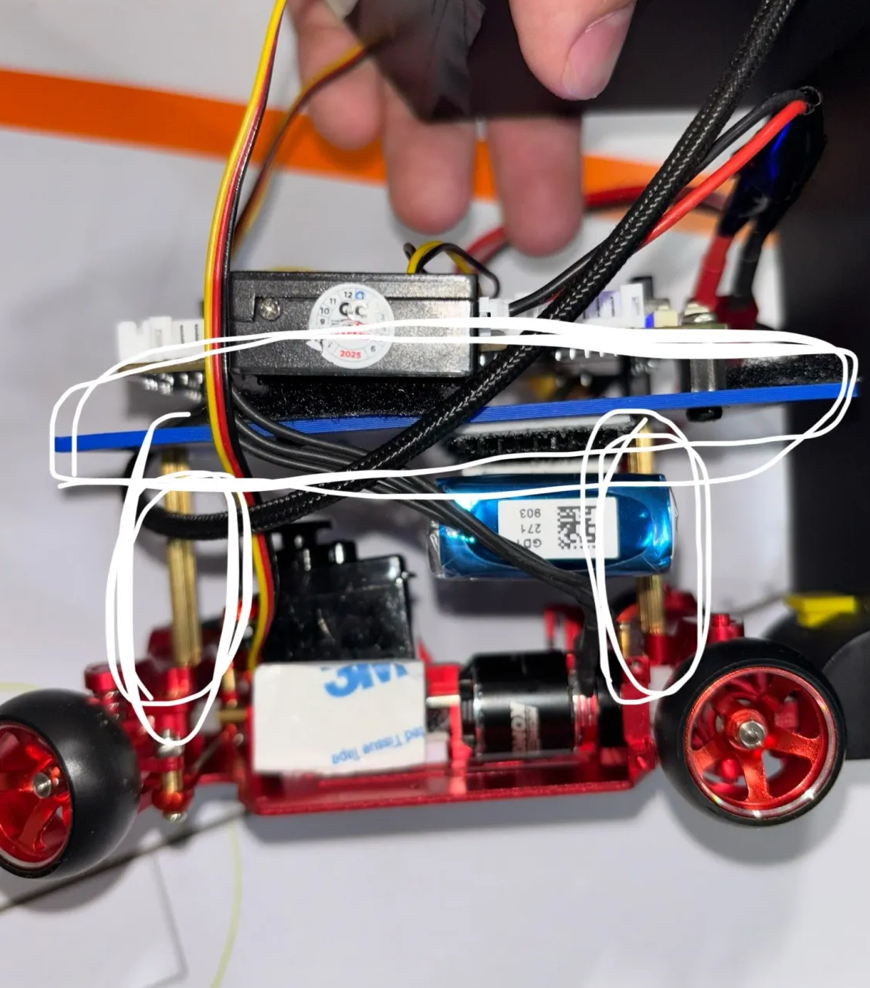
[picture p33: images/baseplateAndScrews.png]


**Back piece**

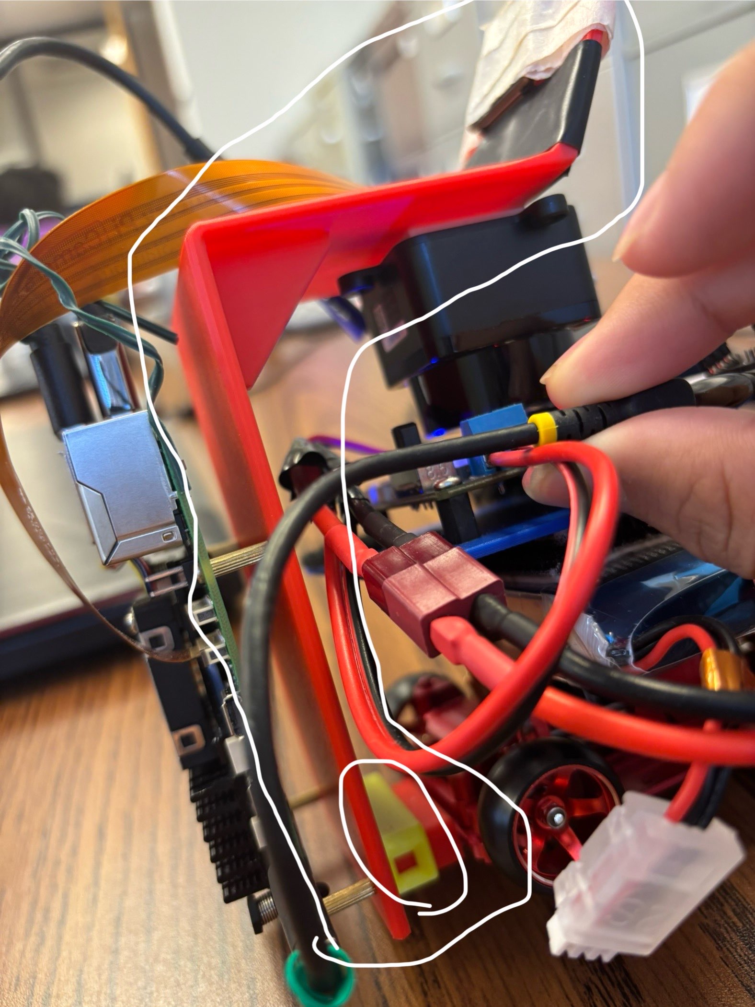
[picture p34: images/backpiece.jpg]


***Fourth step:***
This step will be to attach all the parts that are involved with moving these being the BLDC motor, the servo motor, Raspberry pi 5, and the expansion board.

**Part 1.**
Attaching the servo and BLDC motors. Attach the servo motor with Velcro, and the BLDC motor with the pregiven mount that came along with the chassis.

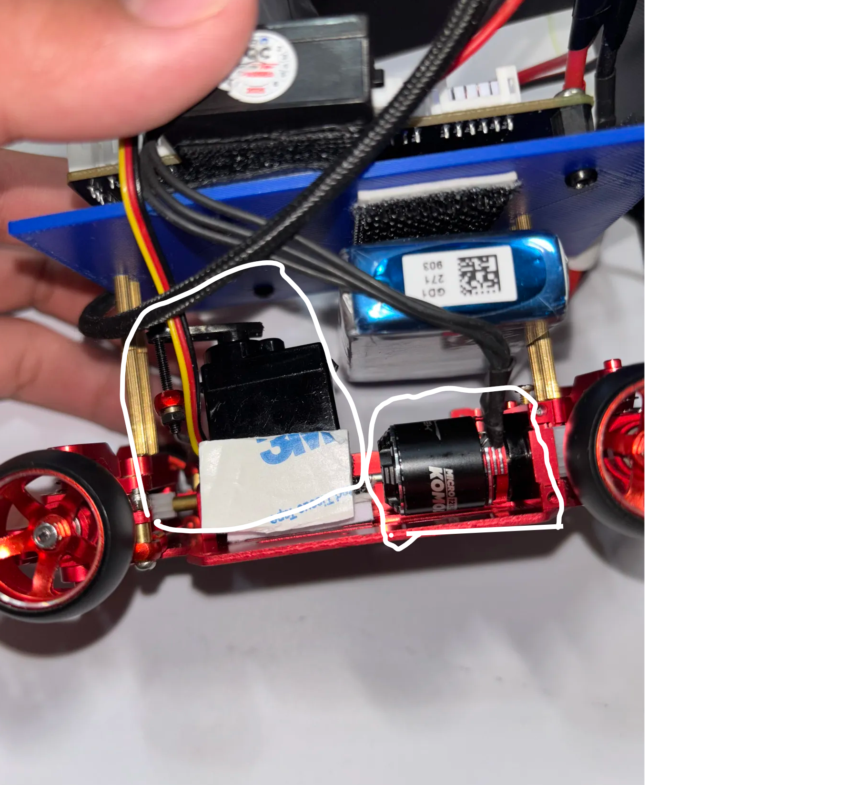
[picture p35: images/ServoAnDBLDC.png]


**Part 2.**
Attaching the Raspberry Pi 5 and the expansion board. Both of these circuits will be screwed into place with screw extenders on each of the four corners in a relatively systematic fashion as each corner for their relative circuit will be the same. The images following will have the circuit encircled and each smaller screw circled also.

**Raspberry Pi 5**

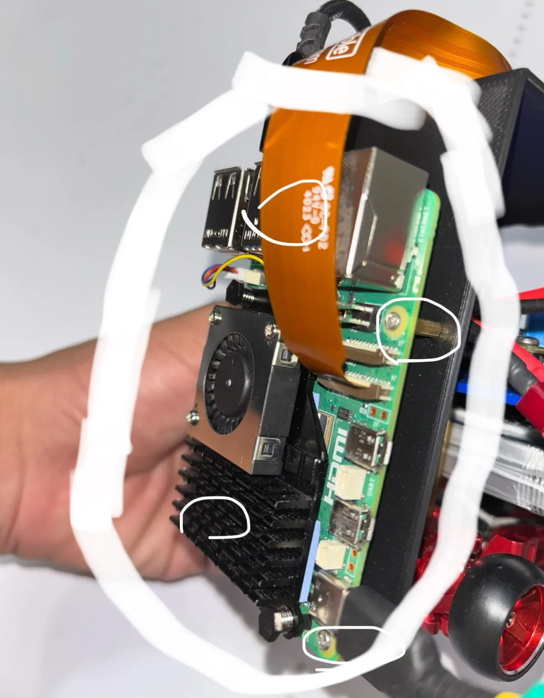
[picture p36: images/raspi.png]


**Expansion Board**



***Fifth Step:***
This step will be to wire everything together; the servo motor goes to the pwm control on the expansion board and the BLDC motor will be connected to an esc which will be Velcroed to the side of the baseplate. This esc will then connect to the switch, the expansion board, and the battery. Next you will need two USB cables, one for data, one for power. The data cable will be USB C to USB A, and the power cable will be USB C to USB C. Next just attach those cables. Finally, as well add a strip of Velcro on the underside of the baseplate. This will be used to attach the battery.

***Sixth Step:***
Step six, we will be adding the lidar and the camera, the camera will be attached to the camera port on the raspberry pi 5 board, for the lidar you will add a piece of double sided tape to the bottom as we will flip it upside down and attach it a little under the camera on the back piece.



***Seventh Step:***
Step seven, attach the battery, beforehand add a strip of velcro to the back of each battery which will conjoin with the underside of the baseplate. After you attach the battery, check all of the connections first before you plug it in. Safety first!!!

***Eight Step:***
Step eight, this step you will have to solder a switch onto the main power cables.

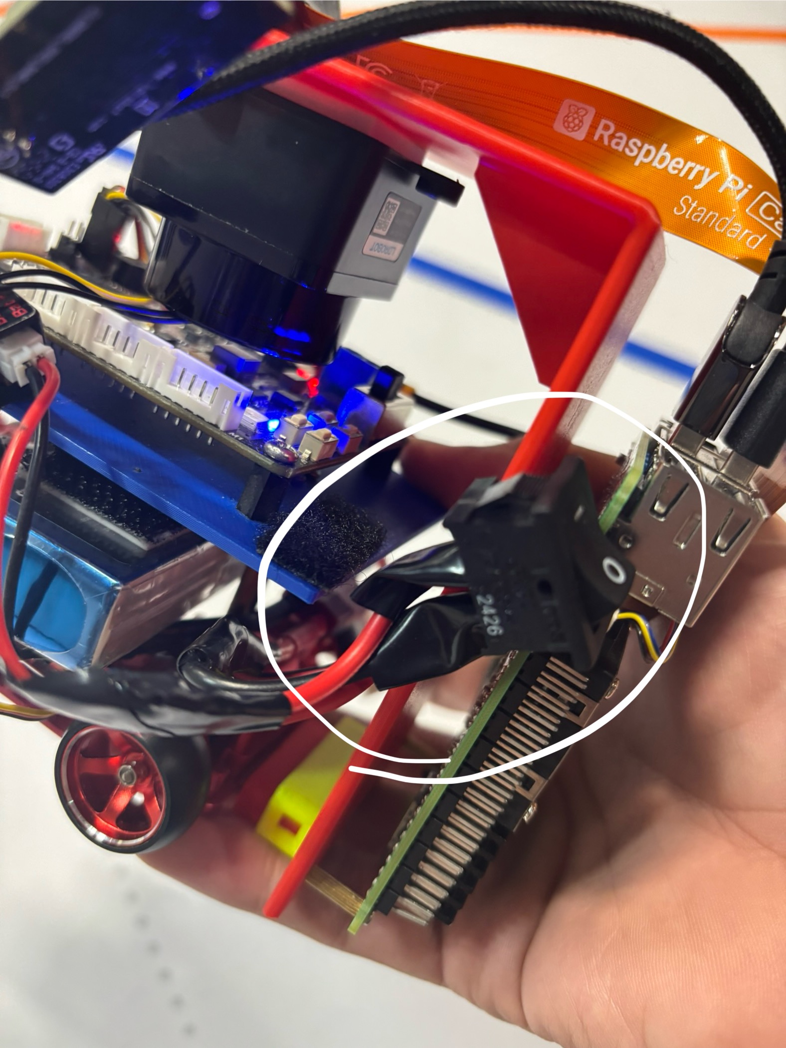
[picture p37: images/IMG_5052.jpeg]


***Nineth Step:***
For step nine you will need to tape the camera cable as well as the camera in place, attach the servo to the servo arm on the chassis, and fix the cables in place with tape or if you have them, zip ties.

***Tenth Step:***
Finally step ten is to just import our code and run it!

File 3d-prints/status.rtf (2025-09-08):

This is a table, in chronological order, that lists the timeline of 3D prints.

Part | Version
Part | v0 | not printed
Part | v1 | printed, didn’t fit, cut off some parts. screw holes too small.
Part | v2 | printed
Part | v3 | not printed, needed screw holes
Baseplate | v4 | printed, printer was bad.
Mount | x1 | printed, base broke off, realized screws didn’t work for this
Baseplate | v5 | printed, changed to allow motor to fit, needed larger holes for mounting ROS extension board.
Baseplate | v6 | printed, but plate is now lifted, so many parts now unnecessary
Mount &Pin | x2 | printed, tolerances too tight for pin hole, slight measurement problems
Mount &Pin | x3 | printed, pin too loose, mount holes for raspberry pi too big
Pins | Testing | printed, .6 perfect
Baseplate | v7 | printed, kinda curved
Mount | x4 | printed, print failure
Baseplate | v8 | printed, holes misaligned
Mount &Pin | x5 | printed, pin disappeared, holes for raspberry pi misaligned
Pin | .565cm | printed, too loose
Baseplate | v9 | printed, very good
Mount &Pin | x6 | printed, needs some fixes
Mount &Pin | x7 | printed, could be more tight
Mount &Pin | x8 | printed, connection slot too tight
Mount &Pin | x9 | printed, mount is good, pin could be improved
Pin | x9.5 | printed, very good

Versions are unique across parts. Parts can have subparts, which are listed after an ampersand.
Final versions: Baseplate v9, Mount x9, Pin @x9.5

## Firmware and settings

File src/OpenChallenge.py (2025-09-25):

import cv2
import lib.ros_robot_controller_sdk as rrc
import time
import numpy as np
from picamera2 import Picamera2 # pyright: ignore[reportMissingImports]
from utils import processContours, imshow, waitKey, destroyAllWindows

ServoChannel = 4
MotorChannel = 1
ServoSpeed = 0.01
MotorTransitionSpeed = 0.1
MaxRightArea = 0
MaxLeftArea = 0
Kp = 0.1
Kd = 0.05
Ki = 0
i_error = 0
stMode = False
stMode_time = -1
stMode_dir = 0
error = 0
last_error = 0
threshold = 60
picam2 = Picamera2()
picam2.configure(
  picam2.create_video_configuration(
    main={"size": (640, 480), "format": "RGB888"},
    sensor={"output_size": (1640, 1232)}
  )
)
picam2.start()
board = rrc.Board()
motorPW = 1620
servoStraight = 1800
servoPW = servoStraight
steer = 0
rate_limit = 1/60
last_time = -1
last_servoPW = -1

lower_orange = np.array([50, 140, 130])
upper_orange = np.array([200, 255, 255])

turnCount = 0
last_turn_detection = -1
detected_turn = False
turn_limit = 12
  
def findContours(image, draw_image=None, *, draw=1, c_colour=None, b_colour=None):
  contours, _hierarchy = cv2.findContours(image, cv2.RETR_EXTERNAL, cv2.CHAIN_APPROX_SIMPLE)
  cntList, MaxCnt, MaxCntArea, _approx, _bounding_box = processContours(contours, 200, draw_image, draw=draw, c_colour=c_colour, b_colour=b_colour)
  return cntList, MaxCnt, MaxCntArea

#Arm the Servo
board.pwm_servo_set_position(ServoSpeed, [[ServoChannel, servoPW]])
time.sleep(1)
start_time = time.time() + 6.28
avg_str = []

while True:
  cur_time = time.time()
  if cur_time - last_time < rate_limit:
    time.sleep((last_time + rate_limit) - cur_time)
  cur_time = time.time()
  dt = cur_time - last_time
  last_time = cur_time

  img = picam2.capture_array()
  ROI_left = img[230:250, 0:300]
  ROI_right = img[230:250, 340:640]
  ROI_front = img[150:480, 70:570]

  ROI_left_grey = cv2.cvtColor(ROI_left, cv2.COLOR_BGR2GRAY)
  ROI_right_grey = cv2.cvtColor(ROI_right, cv2.COLOR_BGR2GRAY)
  ROI_front_lab = cv2.cvtColor(ROI_front, cv2.COLOR_BGR2LAB)
  cv2.rectangle(img, (0, 230), (300, 250), (255, 0, 0), 2)
  cv2.rectangle(img, (340, 230), (640, 250), (255, 0, 0), 2)
  cv2.rectangle(img, (70, 150), (570, 480), (255, 0, 255), 2)

  #imshow("gray", ROI_left_grey)
  ret, imgThresh = cv2.threshold(ROI_left_grey, threshold, 255, cv2.THRESH_BINARY_INV)
  #imshow("threshold", imgThresh)
  leftCntList, MaxLeftCnt, MaxLeftArea = findContours(imgThresh, ROI_left, c_colour=(255, 0, 0), b_colour=(0, 0, 255))

  #imshow("gray", ROI_right_grey)
  ret, imgThresh = cv2.threshold(ROI_right_grey, threshold, 255, cv2.THRESH_BINARY_INV)
  #imshow("threshold", imgThresh)
  rightCntList, MaxRightCnt, MaxRightArea = findContours(imgThresh, ROI_right, c_colour=(255, 0, 0), b_colour=(0, 0, 255))

  mask_orange = cv2.inRange(ROI_front_lab, lower_orange, upper_orange)
  mask_orange = cv2.bitwise_and(mask_orange, (ROI_front_lab[:, :, 2] >= ROI_front_lab[:, :, 1]).astype(np.uint8) * 255)
  imshow("Orange", mask_orange)
  orangeCntList, MaxOrangeCnt, MaxOrangeArea = findContours(mask_orange, ROI_front)

  if turnCount < turn_limit and cur_time - last_turn_detection > (0.4 if detected_turn else 2):
    if MaxOrangeCnt is not None:
      if not detected_turn:
        if MaxOrangeArea > 500 and MaxOrangeArea < 1000:
          detected_turn = True
          last_turn_detection = cur_time
      else:
        if MaxOrangeArea > 1000:
          detected_turn = False
          turnCount += 1
          last_turn_detection = cur_time
  cv2.putText(img, f"Turn detect: {int(detected_turn)}", (490, 25), cv2.FONT_HERSHEY_SIMPLEX, 0.6, (255, 0, 255), 2)
  cv2.putText(img, f"Turn count: {turnCount}", (490, 50), cv2.FONT_HERSHEY_SIMPLEX, 0.6, (255, 0, 0), 2)
  cv2.putText(img, f"Orange area: {MaxOrangeArea}", (470, 75), cv2.FONT_HERSHEY_SIMPLEX, 0.6, (255, 0, 0), 2)

  error = MaxRightArea - MaxLeftArea
  if not stMode:
    i_error += error * dt
  cv2.putText(img, f"Left area: {MaxLeftArea}", (10, 25), cv2.FONT_HERSHEY_SIMPLEX, 0.6, (0, 0, 255), 2)
  cv2.putText(img, f"Right area: {MaxRightArea}", (10, 50), cv2.FONT_HERSHEY_SIMPLEX, 0.6, (0, 255, 0), 2)
  cv2.putText(img, f"Error: {error}", (10, 75), cv2.FONT_HERSHEY_SIMPLEX, 0.6, (255, 0, 255), 2)

  derivative = error - last_error
  last_error = error

  steer = Kp * error + Kd * derivative + Ki * i_error if abs(error) > 0 else 0
  steer = min(300, max(-300, steer))
  if stMode:
    steer = 200 * stMode_dir

  cv2.putText(img, f"Steer: {steer}", (10, 100), cv2.FONT_HERSHEY_SIMPLEX, 0.6, (255, 255, 255), 2)

  servoPW = servoStraight + int(steer)
  if servoPW != last_servoPW:
    board.pwm_servo_set_position(ServoSpeed, [[ServoChannel, servoPW]])
  last_servoPW = servoPW
  #print("servoPW =", servoPW)
  time.sleep(0.01)
  if (MaxLeftArea == 0) ^ (MaxRightArea == 0) and max(MaxLeftArea, MaxRightArea) > 1000 and not stMode:
    stMode = True
    stMode_time = time.time()
    stMode_dir = -1 if MaxRightArea == 0 else 1
    if (len(avg_str) < 5):
      avg_str.append(stMode_dir)
    stMode_dir = int(np.sign(np.average(avg_str)))
    print("Steering Mode ON")
  if stMode and time.time() > stMode_time + 0.5 and \
     MaxLeftArea > 0 and MaxRightArea > 0 and (abs(error) < 500 or (abs(error) * -stMode_dir == error and abs(error) > 500)):
    stMode = False
    last_error = 0
    print("Steering Mode Off")

  imshow("Camera", img)
  if waitKey(1) == ord('q') or (turnCount == turn_limit and cur_time - last_turn_detection > 3):
    motorPW = 1500
    board.pwm_servo_set_position(MotorTransitionSpeed, [[MotorChannel, motorPW]])
    break
  
  if start_time > 0 and time.time() > start_time:
    board.pwm_servo_set_position(MotorTransitionSpeed, [[MotorChannel, motorPW]])
    start_time = -1
destroyAllWindows()

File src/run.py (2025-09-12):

import lib.ros_robot_controller_sdk as rrc
from button_scan import button_queue, wait_for_node
import time
import os

#MODE = "OpenChallenge"
MODE = "ObstacleChallenge"

script_dir = os.path.dirname(__file__)
board = rrc.Board()

wait_for_node(-1)

if MODE == "OpenChallenge":
  board.set_rgb([[1, 0, 0, 63], [2, 0, 0, 63]])
if MODE == "ObstacleChallenge":
  board.set_rgb([[1, 63, 0, 0], [2, 0, 63, 0]])
time.sleep(0.8)

board.set_rgb([[1, 127, 127, 127], [2, 127, 127, 127]])
board.set_buzzer(1950, 0.25, 0.7, 1)

while True:
  button, event = button_queue.get()
  if button != 1: continue
  if event != 1: continue
  if MODE == "OpenChallenge":
    board.set_rgb([[1, 0, 0, 127], [2, 0, 0, 127]])
    time.sleep(0.9)
    board.set_buzzer(1900, 0.1, 0.5, 1)
    time.sleep(0.9)
    board.set_rgb([[1, 0, 0, 0], [2, 0, 0, 0]])
    os.execlp("python3", "python3", script_dir + "/OpenChallenge.py")
  elif MODE == "ObstacleChallenge":
    board.set_rgb([[1, 127, 0, 0], [2, 0, 127, 0]])
    time.sleep(0.9)
    board.set_buzzer(1900, 0.1, 0.5, 1)
    time.sleep(0.9)
    board.set_rgb([[1, 0, 0, 0], [2, 0, 0, 0]])
    os.execlp("python3", "python3", script_dir + "/ObstacleChallenge.py")

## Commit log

2025-05-11 Added circuit diagram files
    [wro schematic circuit.fzz]
2025-05-11 Update README.md - Add circuit diagram
2025-06-23 Adding FuriTek motor to images
2025-07-09 Updated schematics
    [wro schematic circuit.fzz]
2025-08-05 servo motor
2025-08-05 Added servo motor
    added servo motor specifications and picture
2025-08-05 fixed camera price
2025-08-05 Added camera
    added camera instead of "sensor and power management", this includes a camera picture and the specifications
2025-08-09 Add 3D prints
    [Baseplate v4.stl, Baseplate v5.stl, Baseplate v6.stl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]
2025-08-09 servo housing
2025-08-09 servo and bldc pic
2025-08-24 Update README.md
    added step for lidar
2025-08-24 Update README.md
    added picture for lidar
2025-08-24 Adding information to "Our Motor"
2025-08-26 Update README.md
    fixed circuit diagram
2025-08-26 Update README.md
    added lidar price
2025-08-27 Adding the problem with the LIDAR to "challenges we faced"
2025-08-27 Updating Lidar was unreliable section
2025-08-27 Adding Power and Sense Management Section
2025-08-27 Update "Power and Sense Management"
2025-08-29 IMU Code
2025-08-30 added picuter of our first wheels
2025-08-31 Added IMU for steering mode and object detection to avoid collision and wall detection to turn on steering mode when close to wall
    [ObstacleChallenge.py, ObstacleChallengeProcess.py, OpenChallenge.py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]
2025-08-31 Deleting camera and wall follow code explanation
2025-08-31 Adding Potential Improvement of adding voltage regulator
2025-08-31 adding part of lidar code
2025-08-31 Adding potential improvements to the battery
2025-09-01 Update Steering Mode Code
2025-09-06 Adding Potential Improvements to sensors
2025-09-07 added camera code
2025-09-08 Add README.md and update - 3d-prints
    [Pin @x9.5.stl]
2025-09-08 Update README.md - remove nonexisting case
2025-09-12 Changed orange line detection; fixed faulty turnCount initialization.
    [ObstacleChallengeProcess.py]
